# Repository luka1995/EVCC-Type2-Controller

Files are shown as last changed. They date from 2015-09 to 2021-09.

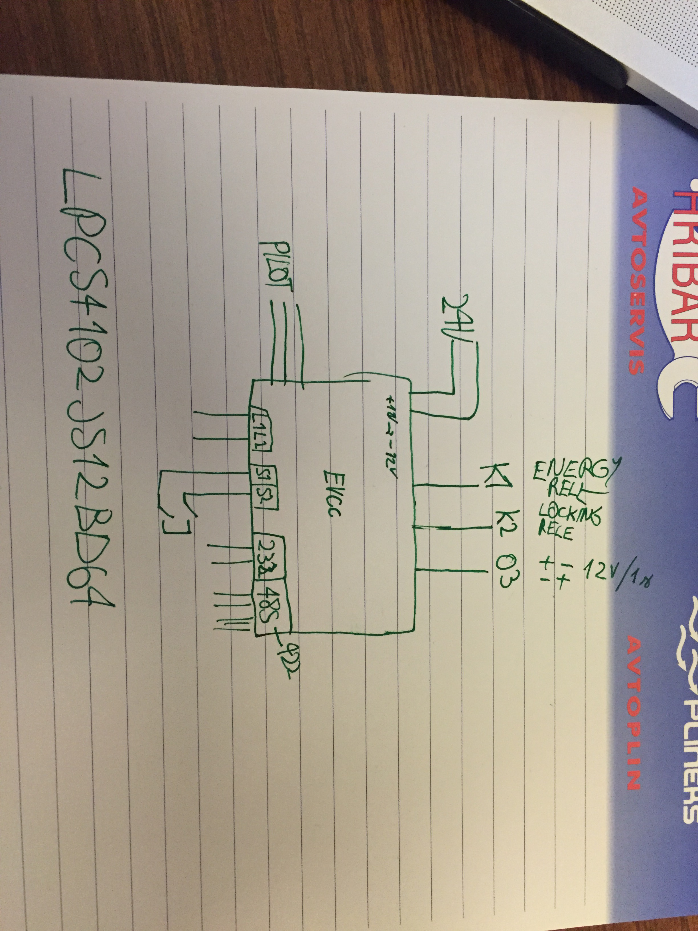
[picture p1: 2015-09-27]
Images/IMG_0896.JPG

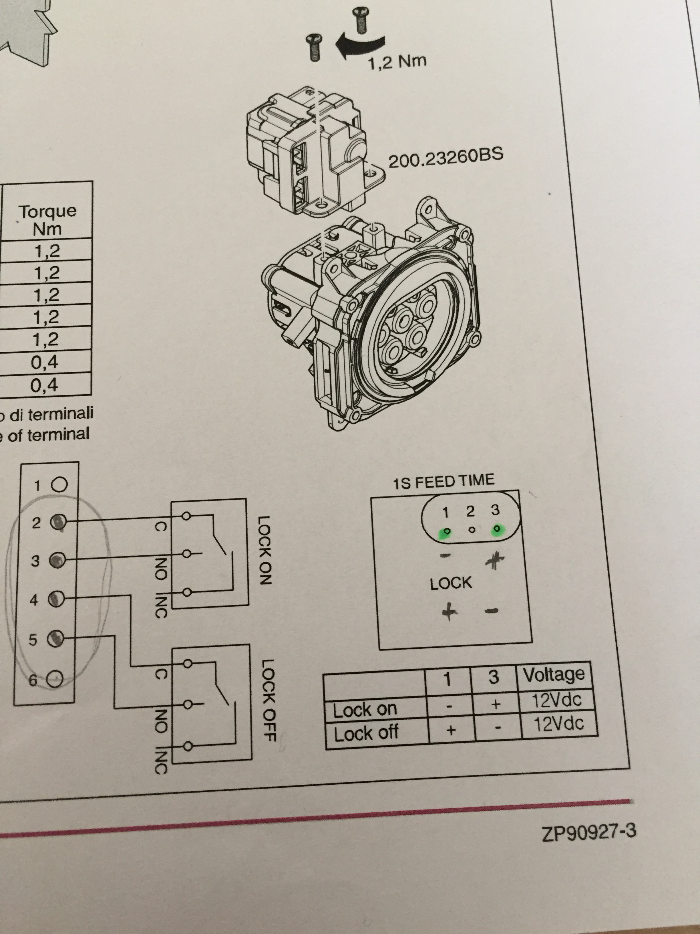
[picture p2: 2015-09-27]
Images/IMG_0889.JPG

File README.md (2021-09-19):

# EVCC TYPE2 Controller

Created by Luka Penger and Duško Cvijič

## Description

The EVCC module controls the power-supply of an electric vehicle (EV) while charging at a supply equipment (EVSE). The communication between EV and EVSE complies with IEC 61851-1 Mode 3.
Potential-free switching contacts are used for load control (EV power-supply) and locking-device (for type 2 socket-outlet). Two external LEDs can be connected without additional resistors and indicate the present system status. Default and available charging current can be set via the RS485 serial interface. The available charging current can be changed while charging, limited by the default current and the rated current of the charging cable (type 2 socket-outlet only).
Start of the charging process and monitoring of the locking mechanism of the socket outlet are controlled by external switches directly connected to the module.
Using the RS485-interface several EVCC can be connected as network with an individual address assigned to each module.

Connector type 2: SAE J1772</br>
Type 2 standard: IEC 61851-1 Mode 3
Serial interface: RS485, 38400Bd, 8 data bits, 1 stop bit, no parity</br>
-> No internal termination; use 120Ω-resistor to terminate both ends of network!

## Proximity voltages:

Max Current
13 A --> Vadc = 2,57 V (R = 1550 ohms)
20 A --> Vadc = 2,22 V (R = 680 ohms)
32 A --> Vadc = 1,82 V (R = 220 ohms)
63 A --> Vadc = 1,66 V (R = 100 ohms)

Not connected --> Vadc = 3.3 V (Max 6A)

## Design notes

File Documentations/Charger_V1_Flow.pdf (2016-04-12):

## Charger Flow V1

Raspberry PI 3
Computer

Type 2 Socket
Connector

Contactor 40A
Switch for energy

Energy Meter
Finder / Class B / 3 Phase

RFID Reader
Mifare / USB
Camera | Ethernet | Wi-Fi
Fuse 3x 40A | Current Circuit Breaker Type B+

EVCC Controller
Type 2

M-Bus Converter
M-Bus to RS-232

Mechanical Fuse
3 x 32A

Main Power
22 kW / 230V

Proximity / Pilot line

Power Supply
230V / 12V

LCD Touch Display
Capacitive / 800 x 480

Fuse 1x 10A

M-Bus

USB Converter
12V / 5V

RS-232

Temperature Sensor
DS18b20

Status Light
SSI

HDMI / USB

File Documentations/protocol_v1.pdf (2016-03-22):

Function | Mode | PC->EVCC | EVCC->PC | Parameter xxxx
Reset device | AM | !n 00 | >n 02 Vx.y | Vx.y Firmware Version
Load factory settings and reset device | AM | !n 01 | >n 02 Vx.y | Vx.y Firmware Version
Get version of firmware | AM | !n 02 | >n 02 Vx.y | Vx.y Firmware Version
Set address of device | AM | !n 03 xxxx | >n 03 | 1…9999
Get address of device | AM | !n 04 | >n 04 xxxx | 1…9999
Get state machine state | AM | !n 05 | >n 05 x | 0 - A1 1 - A2 2 - B1 3 - B2 4 - C1 5 - C2 6 - D1 7 - D2 8 - E 9 - F
Get module mode | AM | !n 06 | >n 06 x | 0 - Auto 1 - Module
Switch mode to MANUAL (Stop charging) | A | !n 07 | >n 07
Switch mode to AUTO (Stop charging) | M | !n 08 | >n 08
Get status of output | AM | !n 09 | >n 09 xx | 0 - all outputs are off 1 - LED1 on 2 - LED2 on 4 - K1 on 8 - K2 on 16 - K3 on …bits
Get status of input | AM | !n 10 | >n 10 x | 0 - non active 1 - S1 active 2 - S2 active 3 - S1 & S2 active …bits
Get ADC value positive pilot | AM | !n 11 | >n 11 xxxx | 0000…4095 U = 0.0xx x xxxx [V]

Commands must end with <CR><LF>.
Answers sent by the module end with <CR><LF>.
n module address (address 0 contacts all modules within the network!).

M state = Manual

A state = Auto

Function | Mode | PC->EVCC | EVCC->PC | Parameter xxxx
Get ADC value negative pilot | AM | !n 12 | >n 12 xxxx | 0000…4095
Get ADC value proximity | AM | !n 13 | >n 13 xxxx | 0000…4095
Get positive pilot voltage | AM | !n 14 | >n 14 xxxx | 0.0…12.0 [V]
Get negative pilot voltage | AM | !n 15 | >n 15 xxxx | 0.0…-12.0 [V]
Get proximity voltage | AM | !n 16 | >n 16 xxxx | 0.0…3.3 [V]
Get Ic - PWM duty cycle | AM | !n 17 | > 17 xxx | 80…970 - PWM value 8%…97%
Set Ic max | M | !n 18 xxx | >n 18 | 0 - 6A 1 - 10A 2 - 13A 3 - 16A 4 - 20A 5 - 32A 6 - 40A 7 - 50A 8 - 60A 9 - 70A 10 - 80A 11 - Idefault 80…970 - PWM value 8%…97%
Set Idefault | M | !n 19 xxx | >n 19 | 0 - 6A 1 - 10A 2 - 13A 3 - 16A 4 - 20A 5 - 32A 6 - 40A 7 - 50A 8 - 60A 9 - 70A 10 - 80A 80…970 - PWM value 8%…97%
Get Idefault | AM | !n 20 | >n 20 xxx | 80…970 - PWM value 8%…97%
Switch PWM on | M | !n 21 | >n 21
Switch PWM off | M | !n 22 | >n 22
Get PWM state | AM | !n 23 | >n 23 x | 0 - OFF 1 - ON
Start charging | M | !n 24 | >n 24
Stop charging | M | !n 25 | >n 25

Function | Mode | PC->EVCC | EVCC->PC | Parameter xxxx
Enable proximity cable detection max current | AM | !n 26 | >n 26
Disable proximity cable detection max current | AM | !n 27 | >n 27
Get proximity cable detection state | AM | !n 28 | >n 28 | 0 - OFF 1 - ON

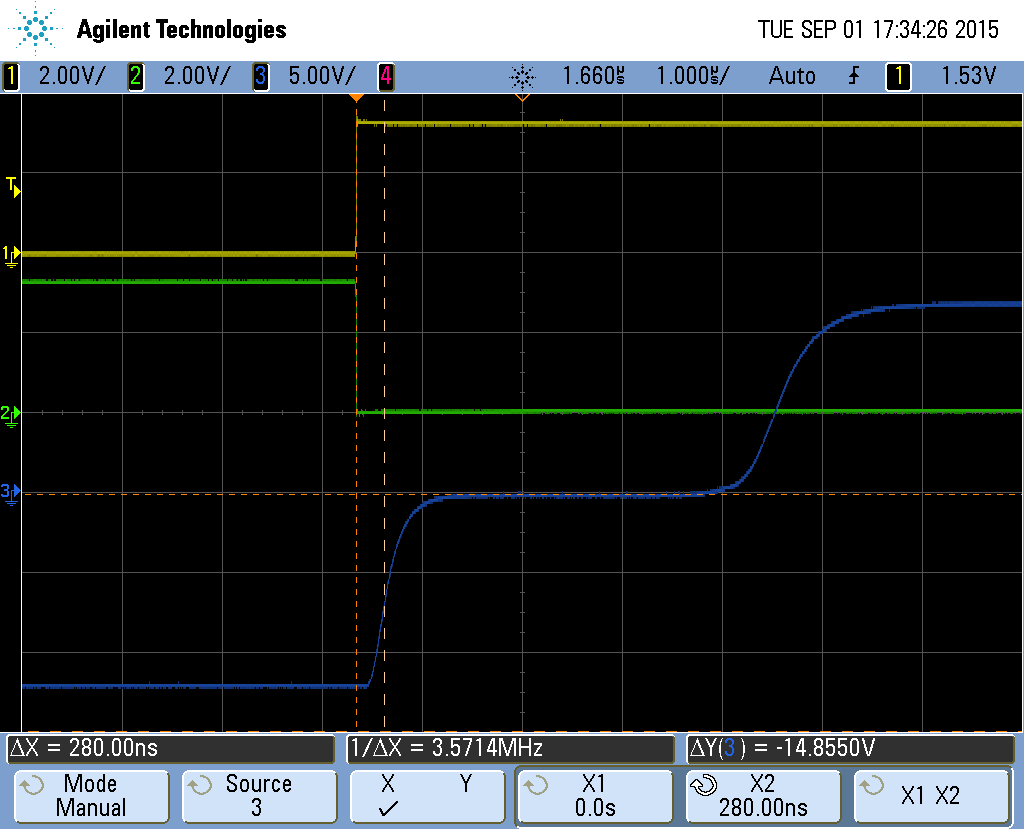
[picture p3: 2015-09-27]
Images/scope_0.bmp

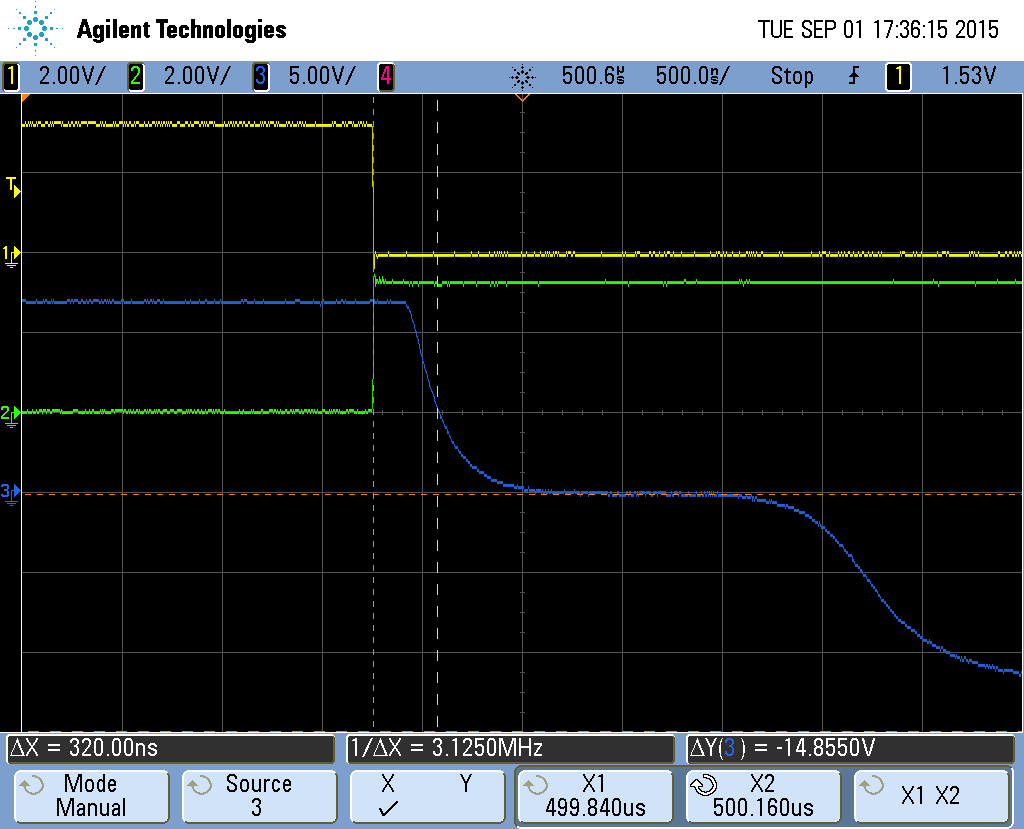
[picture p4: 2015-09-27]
Images/scope_2.bmp

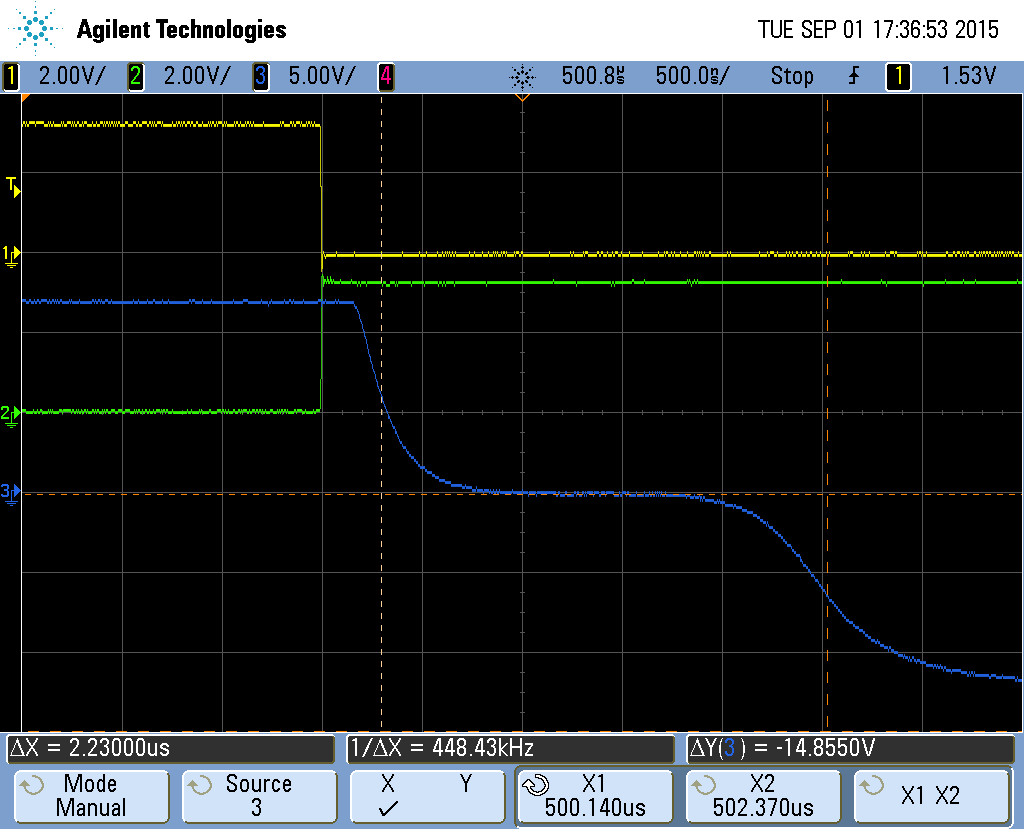
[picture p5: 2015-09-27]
Images/scope_3.bmp

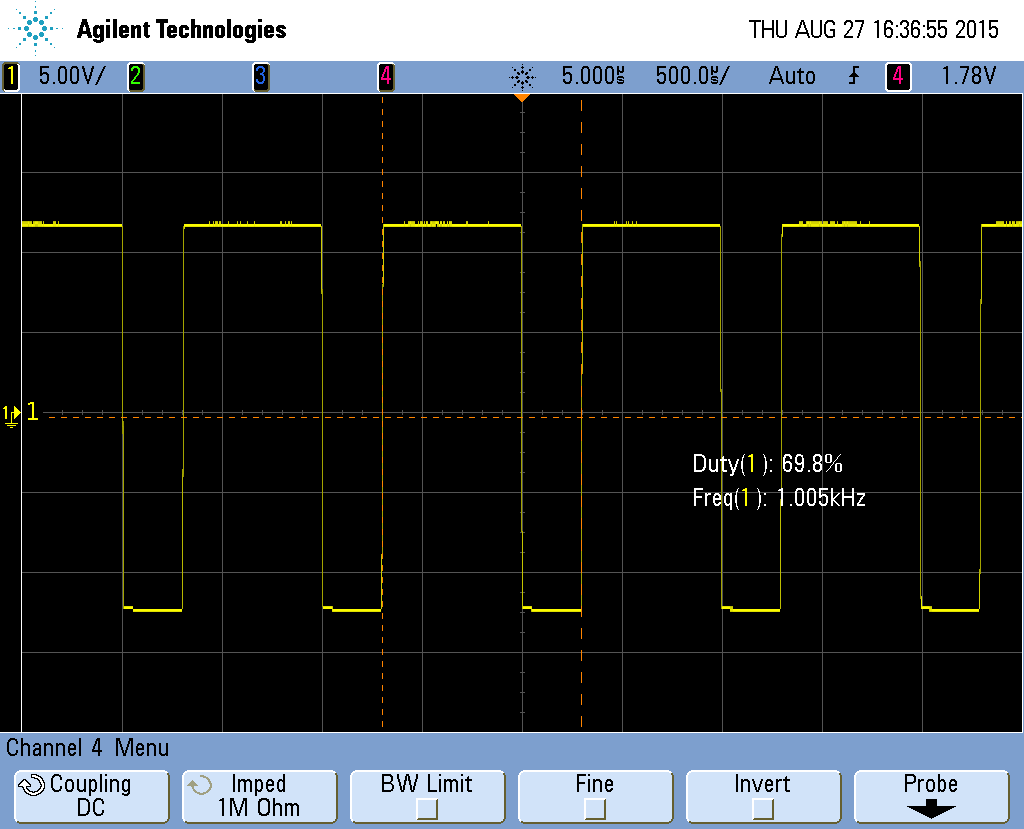
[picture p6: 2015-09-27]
Images/pwm_70.bmp

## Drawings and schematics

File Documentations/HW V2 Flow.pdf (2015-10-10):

## EVCC TYPE2 Controller Hardware V2

### Main power supply

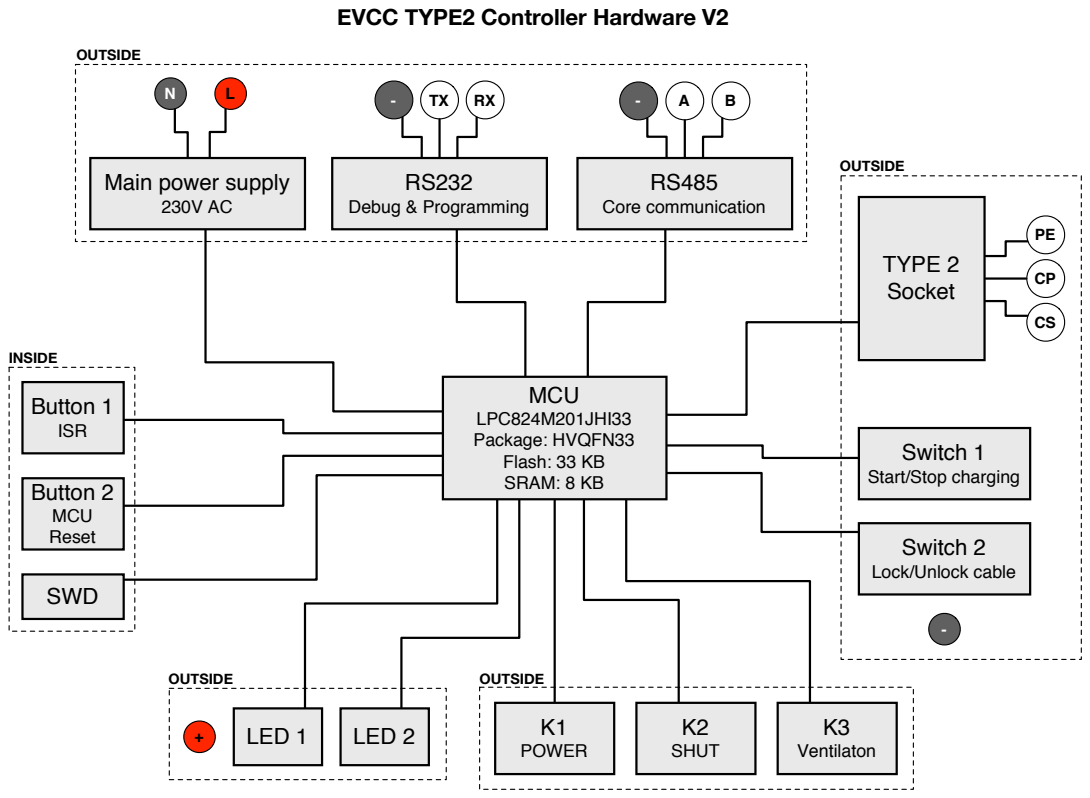
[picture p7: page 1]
MCU LPC824M201JHI33 Package: HVQFN33 Flash: 33 KB SRAM: 8 KB; RS232 Debug & Programming; RS485 Core communication; Button 1 ISR; Button 2 MCU Reset; SWD; TYPE 2 Socket; LED 1; LED 2; K1 POWER; K2 SHUT; K3 Ventilaton; INSIDE; OUTSIDE

Switch 1
Start/Stop charging

Switch 2
Lock/Unlock cable

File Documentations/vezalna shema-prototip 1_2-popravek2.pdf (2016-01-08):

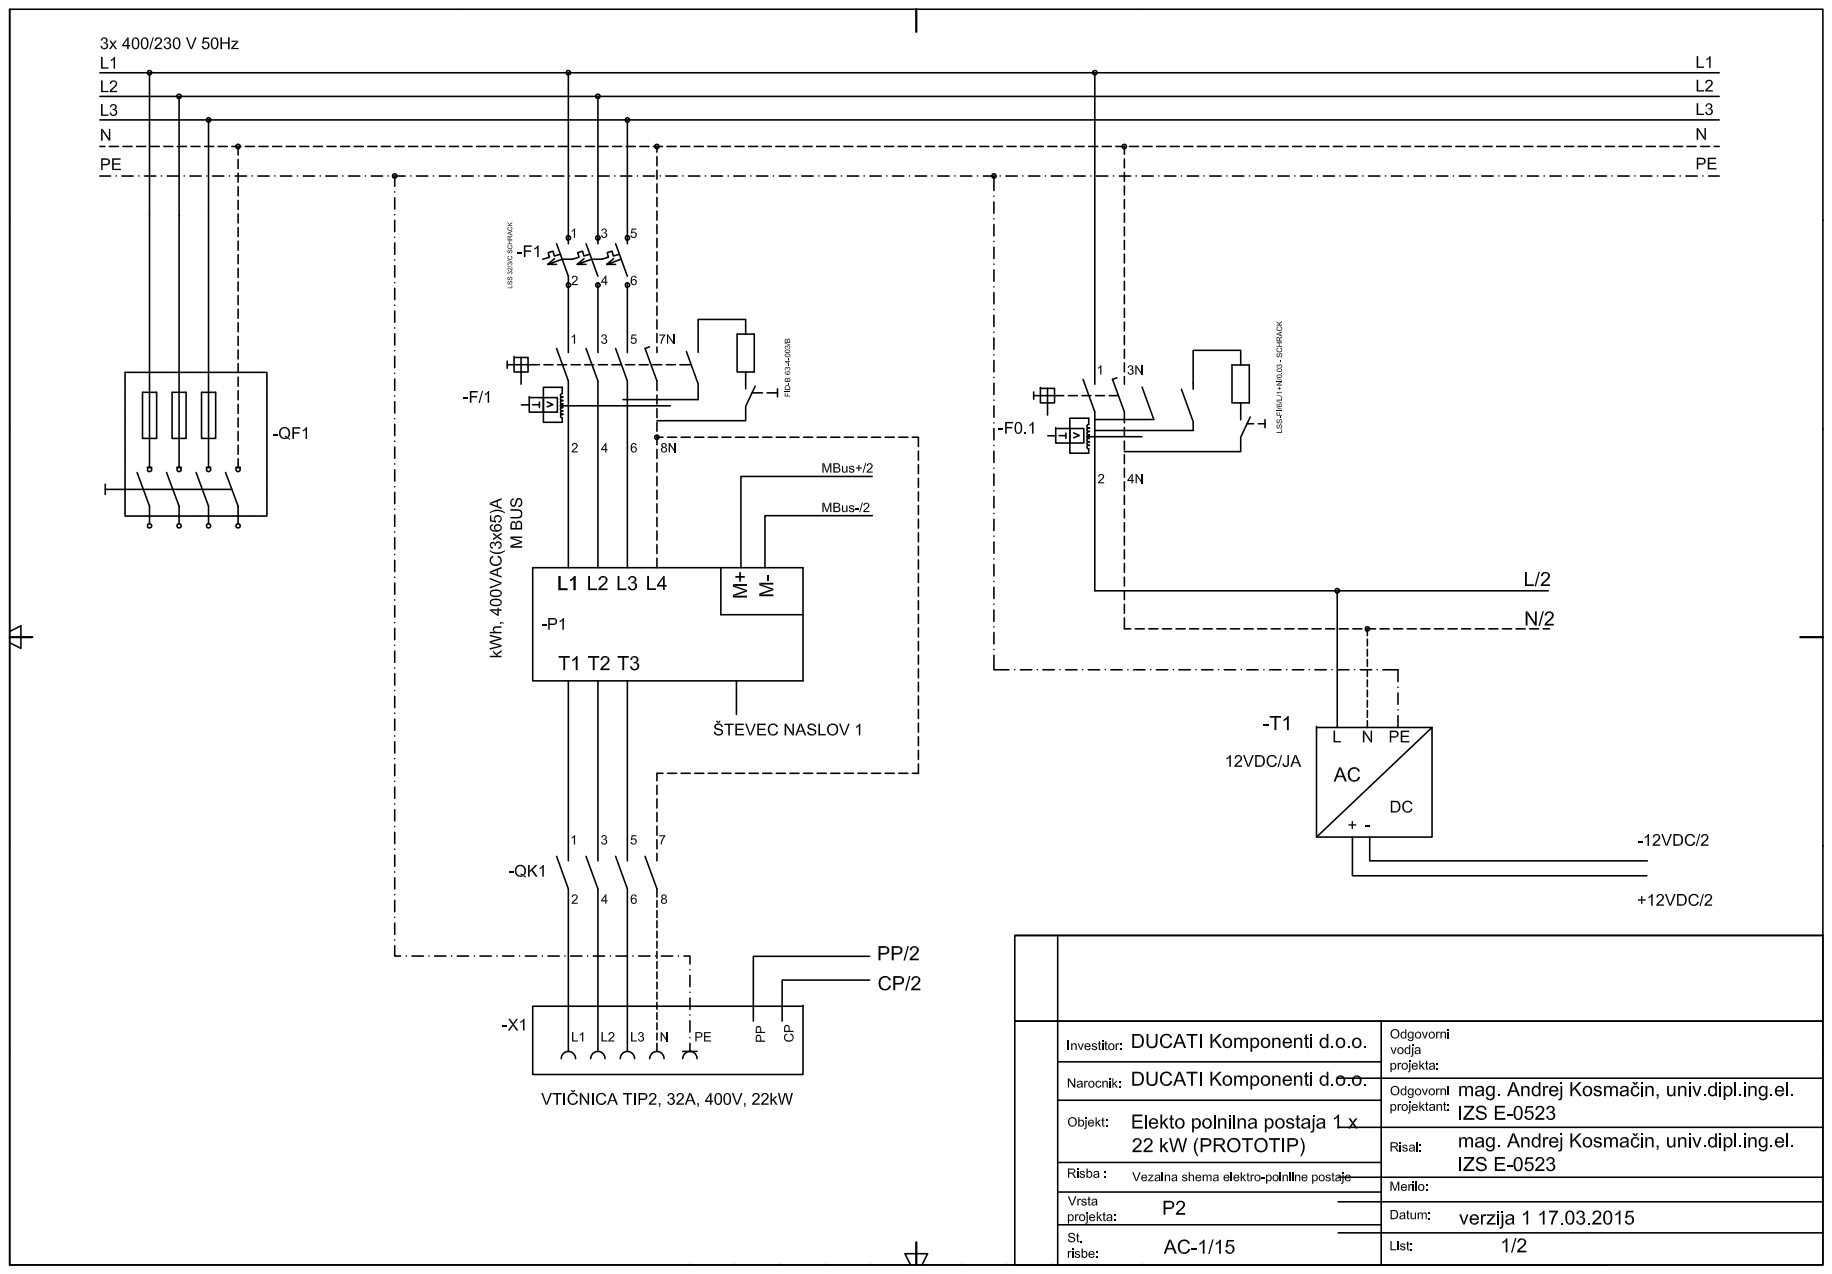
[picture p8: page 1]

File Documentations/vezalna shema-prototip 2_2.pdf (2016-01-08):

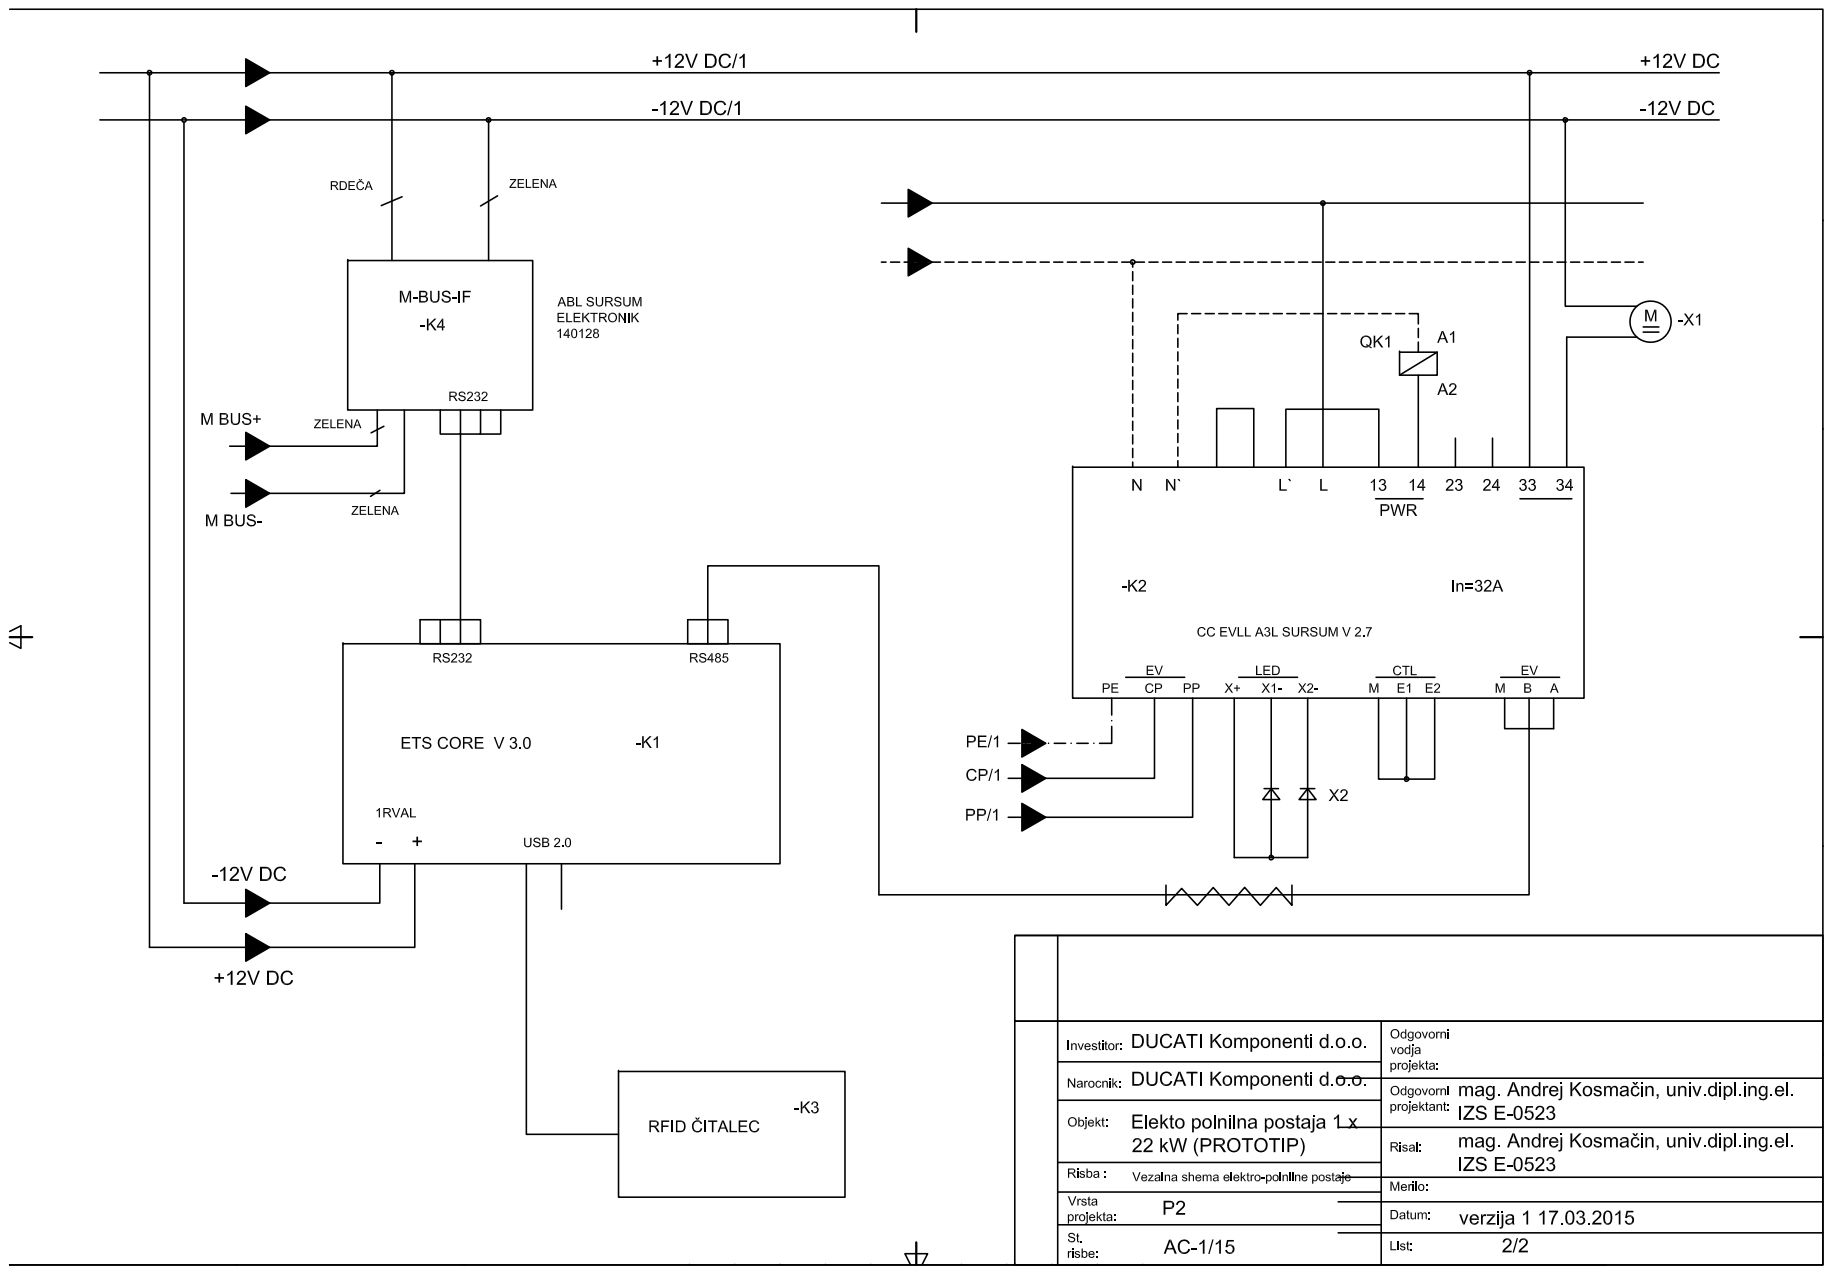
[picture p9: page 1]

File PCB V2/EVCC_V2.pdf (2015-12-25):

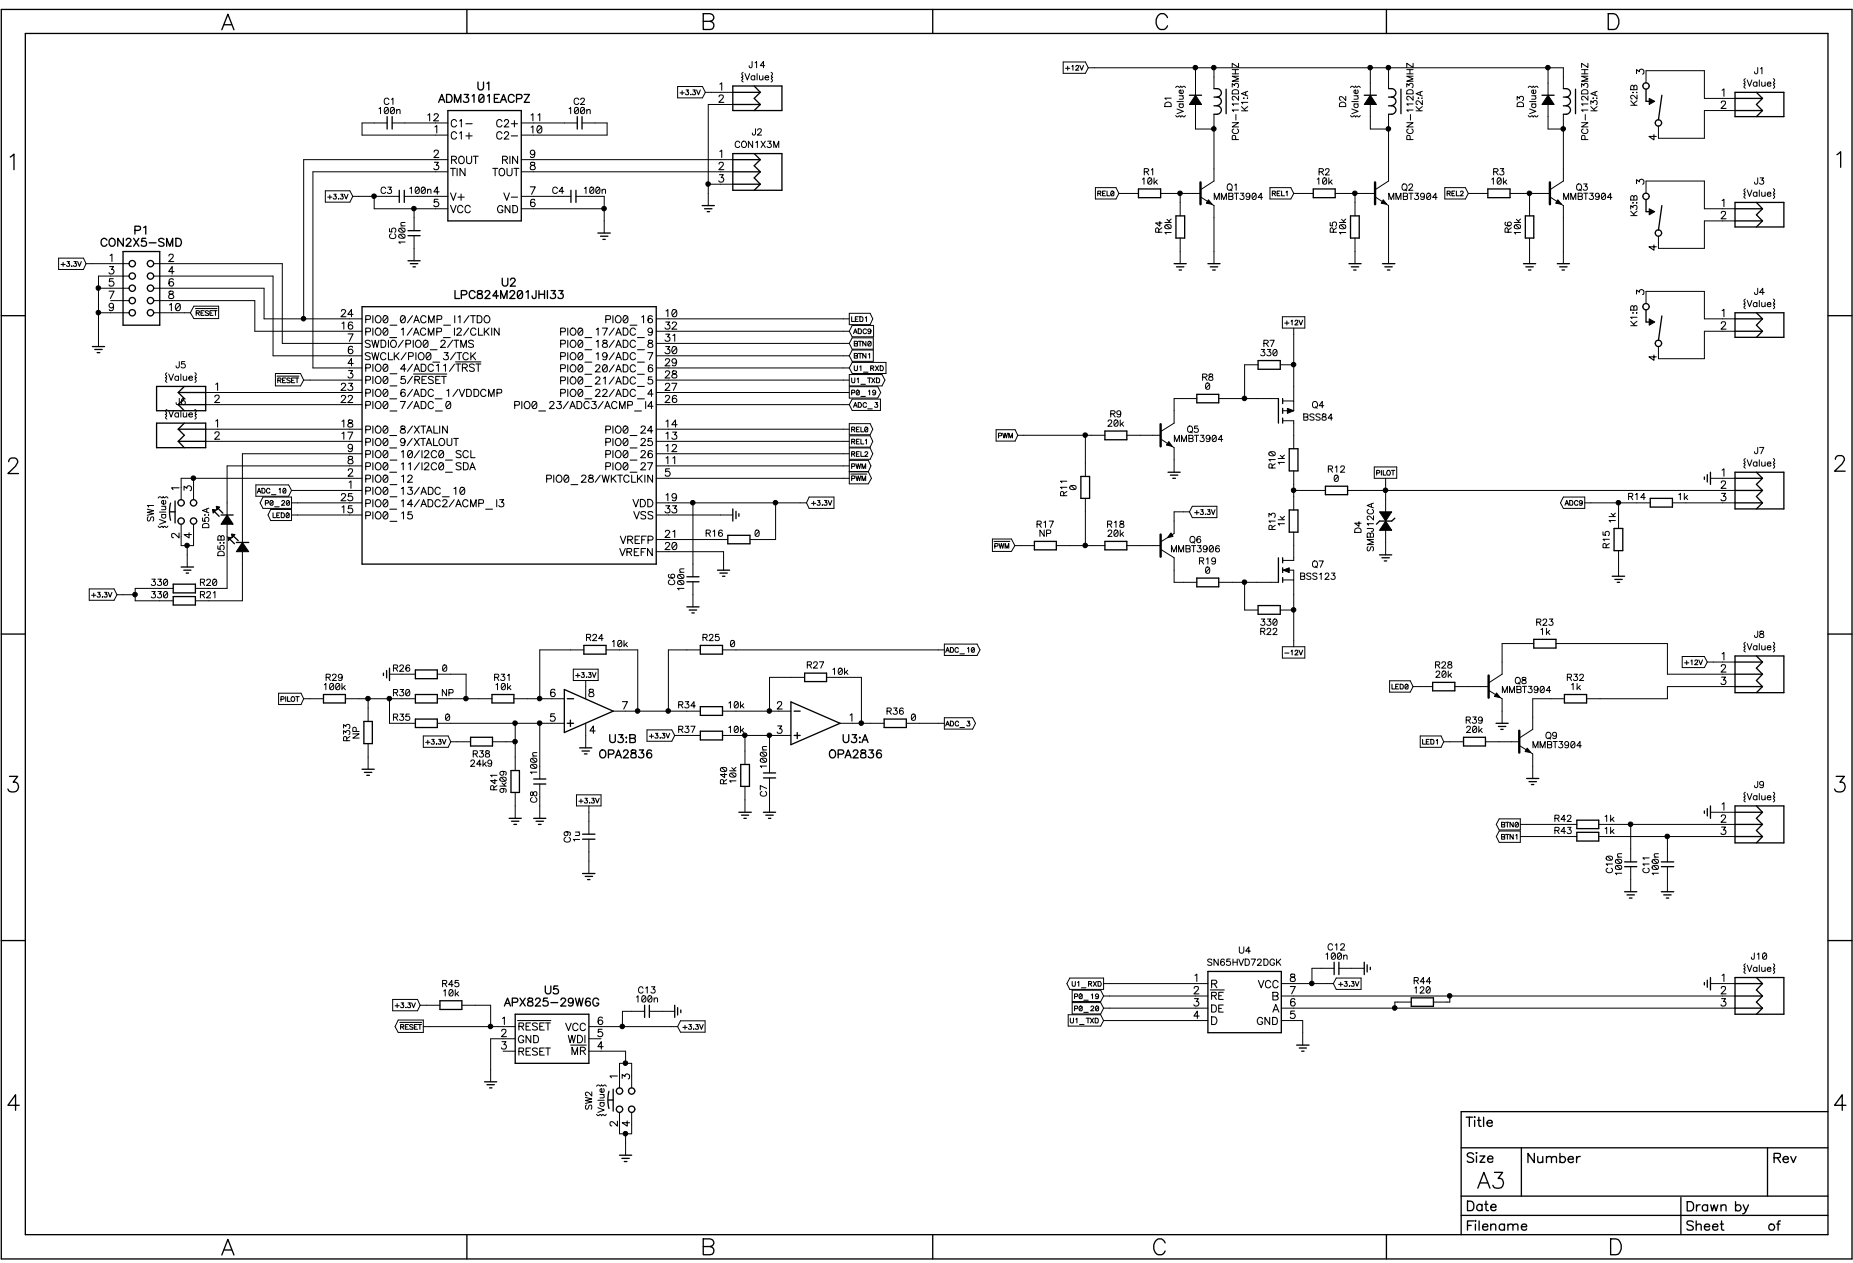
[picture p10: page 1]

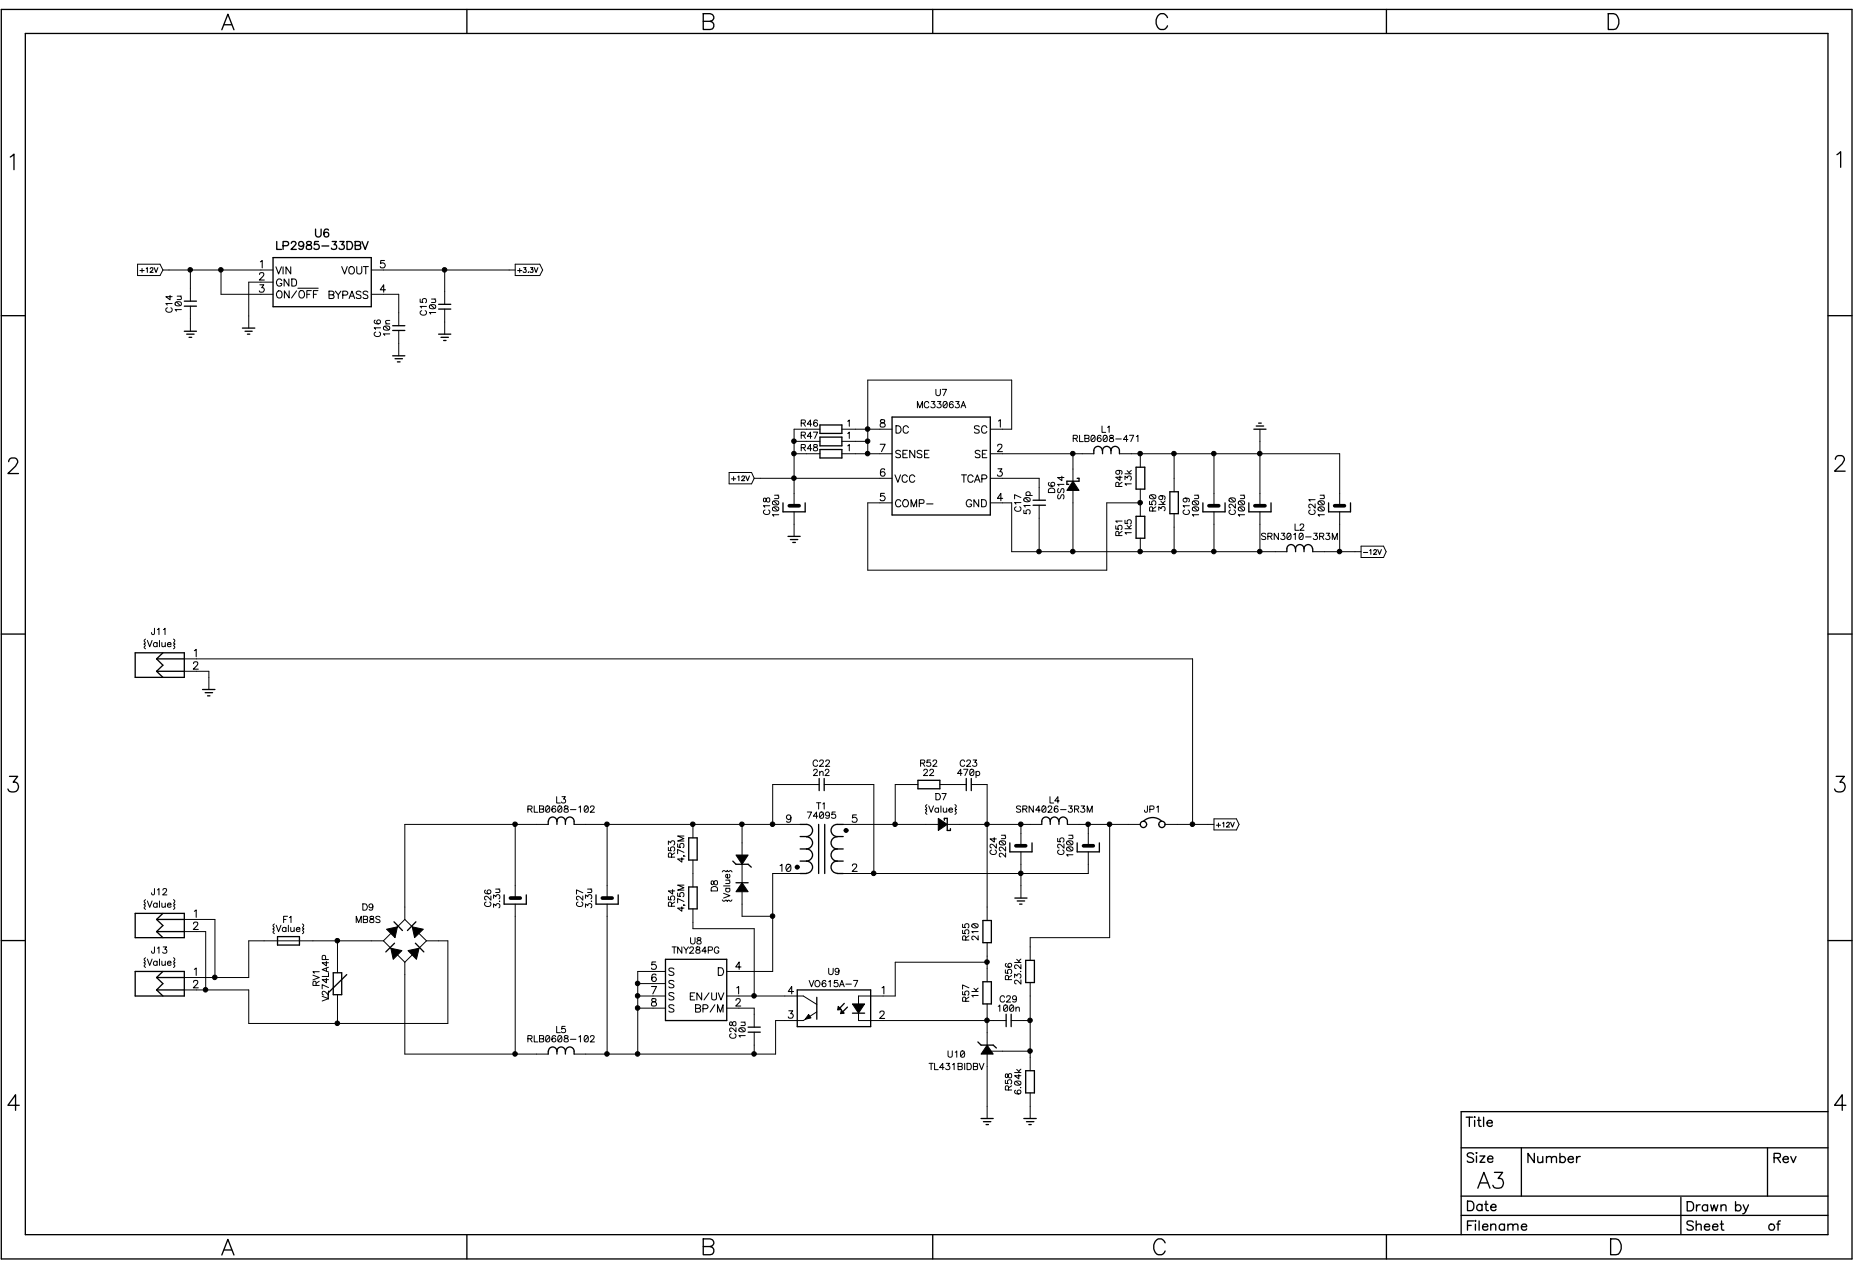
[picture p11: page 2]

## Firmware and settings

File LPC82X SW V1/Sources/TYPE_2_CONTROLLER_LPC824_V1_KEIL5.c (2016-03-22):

/*----------------------------------------------------------------------------
 *      Type 2 Controller LPC824
 *			Copyright 2015
 *			Luka Penger
 *			Avant Car d.o.o.
 *---------------------------------------------------------------------------*/

#include <stdio.h>
#include <stdint.h>
#include <stdbool.h>
#include <stddef.h>
#include <ctype.h>
#include <LPC82x.h>

#include "cmsis_os.h"
#include <GPIO_LPC82x.h>
#include <ADC_LPC82x.h>
#include <IAP_LPC82x.h>
#include <WWDT_LPC82x.h>
#include "SETTINGS.h"
#include "EV_UART.h"
#include "EV_PWM.h"
#include "EV_ADC.h"
#include "EV_STATE_MACHINE.h"
#include "EV_OUTPUTS.h"
#include "EV_INPUTS.h"

/*****************************************************************************
 * Definitions
 ****************************************************************************/

#define FIRMWARE_VERSION												"1.0"

#define DEFAULT_MODULE_ADDRESS									0
#define MODULE_ADDRESS_MAX_NUMBER								9999

#define ADC_SAMPLE_INTERVAL											100 // ms / when pwm = false
#define STATE_MACHINE_INTERVAL									50 // ms

/*****************************************************************************
 * Public variables
 ****************************************************************************/

extern SETTINGS_Struct settingsData;

extern EvModuleMode selectedModuleMode;

extern char EV_UART_Buffer[EV_UART_BUFFER_SIZE];
extern int EV_UART_BufferLength;
extern bool EV_UART_DataReceived;

extern float selectedMaximumCurrent;
extern bool pwmRunning;
extern float evPwmDutyCycle;

extern bool sequenceAComplete, sequenceBComplete;
extern bool groundError;
extern unsigned int proximityADCValue; // 0 - 4095
extern unsigned int pilotPositiveADCValue; // 0 - 4095
extern unsigned int pilotNegativeADCValue; // 0 - 4095
extern float proximityVoltage; // 0.0V - 3.3V
extern float pilotPositiveVoltage; // 0.0V - 12.0V
extern float pilotNegativeVoltage; // 0.0V - -12.0V
extern bool adcCPVoltageMeasured, adcPPVoltageMeasured;

extern void (*currentStateMachine)(void);
extern int evStateMachineWaitMs;
extern bool manualStartChargingFlag;

int ledWaitMs = 0;

/*****************************************************************************
 * Watchdog Timer
 ****************************************************************************/

void WDT_IRQHandler(void) {
	uint32_t wdtStatus = WWDT_GetStatus(LPC_WWDT);
	
	/* The chip will reset before this happens, but if the WDT doesn't
	   have WWDT_WDMOD_WDRESET enabled, this will hit once */
	if (wdtStatus & WWDT_WDMOD_WDTOF) {
		/* A watchdog feed didn't occur prior to window timeout */
		WWDT_UnsetOption(LPC_WWDT, WWDT_WDMOD_WDEN);	/* Stop WDT */
		WWDT_ClearStatusFlag(LPC_WWDT, WWDT_WDMOD_WDTOF);
		WWDT_Start(LPC_WWDT);	/* Needs restart */
	}

	/* Handle warning interrupt */
	if (wdtStatus & WWDT_WDMOD_WDINT) {
		/* A watchdog feed didn't occur prior to warning timeout */
		WWDT_ClearStatusFlag(LPC_WWDT, WWDT_WDMOD_WDINT);
		WWDT_Feed(LPC_WWDT);
	}
}

void Watchdog_Init(void) {
	uint32_t wdtFreq;
	
	/* Freq = 0.6Mhz, divided by 64. WDT_OSC should be 9.375khz */
	Clock_SetWDTOSC(WDTLFO_OSC_0_60, 64);
	
	SYSCTL_PowerUp(SYSCTL_SLPWAKE_WDTOSC_PD);

	wdtFreq = (Clock_GetWDTOSCRate() / 4);
	
	WWDT_Init(LPC_WWDT);

	/* Set watchdog feed time constant to approximately 2s
	   Set watchdog warning time to 512 ticks after feed time constant
	   Set watchdog window time to 3s */
	WWDT_SetTimeOut(LPC_WWDT, wdtFreq * 2);
	WWDT_SetWarning(LPC_WWDT, 512);
	WWDT_SetWindow(LPC_WWDT, wdtFreq * 3);

	/* Configure WWDT to reset on timeout */
	WWDT_SetOption(LPC_WWDT, WWDT_WDMOD_WDRESET);

	/* Clear watchdog warning and timeout interrupts */
	WWDT_ClearStatusFlag(LPC_WWDT, WWDT_WDMOD_WDTOF | WWDT_WDMOD_WDINT);

	/* Clear and enable watchdog interrupt */
	NVIC_ClearPendingIRQ(WDT_IRQn);
	NVIC_EnableIRQ(WDT_IRQn);

	/* Start watchdog */
	WWDT_Start(LPC_WWDT);
}

/*****************************************************************************
 * Public functions
 ****************************************************************************/


/*****************************************************************************
 * Private functions
 ****************************************************************************/

void init(void) {
	SystemInit();
	SystemCoreClockUpdate();
	
	/*
	1 = 1s
	10 = 100ms
	100 = 10ms
	1000 = 1ms*/
	SysTick_Config(SystemCoreClock / 1000);
	
	// WWDT Init
	
	Watchdog_Init();
	
	// EV Init
	
	EV_OUTPUTS_Init();
	
	EV_INPUTS_Init();

	EV_UART_Init();
	
	EV_PWM_Init();
	
	EV_ADC_Init();
	
	// Settings load
	
	SETTINGS_Load();
	
	// Default state machine
	
	EV_State_A1();
}

/*****************************************************************************
 * Main
 ****************************************************************************/

int main(void) {
	//
	// Variables
	//
	char *evUartModuleAddressString = NULL, *evUartFunctionString = NULL, *evUartValueString = NULL;
	int evUartModuleAddressSpaceIndex = 0, evUartFunctionSpaceIndex = 0;
	int evUartModuleAddressNumber = 0, evUartFunctionNumber = 0, evUartValueNumber = 0;
	bool evUartShowCommandError = false;
	int sysTickAdcSampleValue = 0, sysTickStateMachineValue = 0;
	
	//
	// Init
	//
 	init();
	
	// Send firmware version
	
	EV_UART_SendStringFormat("%c%d %02d", EV_UART_SEND_CHARACTER, settingsData.selectedModuleAddress, 2);
	EV_UART_SendString(" V"FIRMWARE_VERSION);
	EV_UART_SendString("\r\n");
	
	// Set maximum current
	
	selectedMaximumCurrent = settingsData.selectedIdefault;
	EV_PWM_SetDutyCycle(selectedMaximumCurrent);
	
	//
	// While
	//
	while (1) {
		/*****************************************************************************
		* ADC Voltage Read
		****************************************************************************/
		
		if (sequenceAComplete == true) {
			sequenceAComplete = false; // Clear flag
			
			// Read CP Voltage
			
			EV_ADC_ReadCPVoltage();
	  }
		
		if (sequenceBComplete == true) {
			sequenceBComplete = false; // Clear flag
			
			// Read PP Voltage
			
			EV_ADC_ReadPPVoltage();
	  }
		
		/*****************************************************************************
		* SysTick Value Listener
		****************************************************************************/

		if (SysTick->CTRL & SysTick_CTRL_COUNTFLAG_Msk) {
			// ADC Sequencer
			
			if (sysTickAdcSampleValue >= ADC_SAMPLE_INTERVAL) {
				sysTickAdcSampleValue = 0; // Clear flag

				if (pwmRunning == false) {
					ADC_StartSequencer(LPC_ADC, ADC_SEQA_IDX);
				}
				
				ADC_StartSequencer(LPC_ADC, ADC_SEQB_IDX);
			} else {
				sysTickAdcSampleValue++;
			}
			
			// EV State Machine
			
			if (adcCPVoltageMeasured && sysTickStateMachineValue >= STATE_MACHINE_INTERVAL) {
				sysTickStateMachineValue = 0; // Clear flag

				// State machine
			
				EV_State_Machine();
			} else {
				sysTickStateMachineValue++;
			}
			
			if (evStateMachineWaitMs > 0) {
				evStateMachineWaitMs--;
			}
			
			// LED States
			
			if (ledWaitMs == 0) {
				if (currentStateMachine == EV_State_A1 || currentStateMachine == EV_State_A2) {
					ledWaitMs = 1000; // Only for disable setting led no 1ms
					
					EV_OUTPUTS_SetLED2(false);
					EV_OUTPUTS_SetLED1(false);
				} else if (currentStateMachine == EV_State_B1 || currentStateMachine == EV_State_B2) {
					ledWaitMs = 1000; // Only for disable setting led no 1ms
					
					EV_OUTPUTS_SetLED2(false);
					EV_OUTPUTS_SetLED1(true);
				} else if (currentStateMachine == EV_State_C1 || currentStateMachine == EV_State_C2) {
					ledWaitMs = 1000; // Only for disable setting led no 1ms
					
					EV_OUTPUTS_SetLED2(true);
					EV_OUTPUTS_SetLED1(false);
				} else if (currentStateMachine == EV_State_D1 || currentStateMachine == EV_State_D2) {
					ledWaitMs = 1000;
					
					EV_OUTPUTS_SetLED1(false);
					
					if (EV_OUTPUTS_GetStateLED2()) {
						EV_OUTPUTS_SetLED2(false);
					} else {
						EV_OUTPUTS_SetLED2(true);
					}
				} else if (currentStateMachine == EV_State_E || currentStateMachine == EV_State_F) {
					ledWaitMs = 2000;
					
					if (EV_OUTPUTS_GetStateLED1()) {
						EV_OUTPUTS_SetLED2(false);
						EV_OUTPUTS_SetLED1(false);
					} else {
						EV_OUTPUTS_SetLED2(true);
						EV_OUTPUTS_SetLED1(true);
					}
				}
			} else {
				ledWaitMs--;
			}
		}
		
		/*****************************************************************************
		* EV UART Listener
		****************************************************************************/
		
		if (EV_UART_DataReceived == true && (UART_GetStatus(EV_UART) & UART_STAT_RXIDLE) != 0 && (UART_GetStatus(EV_UART) & UART_STAT_RXRDY) == 0) {
			EV_UART_DataReceived = false;

			// Search MODULE ADDRESS space index
			evUartModuleAddressSpaceIndex = EV_UART_LocateCharacter(EV_UART_Buffer, EV_UART_BufferLength, 0x20, 0);
			
			if (evUartModuleAddressSpaceIndex > 0) {
				evUartModuleAddressString = (char *)malloc(evUartModuleAddressSpaceIndex);
				strncpy(evUartModuleAddressString, EV_UART_Buffer, evUartModuleAddressSpaceIndex);
				
				if (EV_UART_BufferIsNumber(evUartModuleAddressString, evUartModuleAddressSpaceIndex) == true) {
					evUartModuleAddressNumber = atoi(evUartModuleAddressString);
					
					// Free pointer
					if (evUartModuleAddressString != NULL) { free(evUartModuleAddressString); evUartModuleAddressString = NULL; }
					
					// Check module address if correct
					if (evUartModuleAddressNumber == DEFAULT_MODULE_ADDRESS || evUartModuleAddressNumber == settingsData.selectedModuleAddress) {
						// MODULE ADDRESS IS CORRECT

						// Search FUNCTION space index
						evUartFunctionSpaceIndex = EV_UART_LocateCharacter(EV_UART_Buffer, EV_UART_BufferLength, 0x20, 1);
						
						if (evUartFunctionSpaceIndex > 0) {
							evUartFunctionString = (char *)malloc(evUartFunctionSpaceIndex - (evUartModuleAddressSpaceIndex + 1));
							strncpy(evUartFunctionString, EV_UART_Buffer + (evUartModuleAddressSpaceIndex + 1), (evUartFunctionSpaceIndex - (evUartModuleAddressSpaceIndex + 1)));
							
							// COMMAND WITH VALUE
							if (EV_UART_BufferIsNumber(evUartFunctionString, (evUartFunctionSpaceIndex - (evUartModuleAddressSpaceIndex + 1))) == true) {
								evUartFunctionNumber = atoi(evUartFunctionString);
								
								// Free pointer
								if (evUartFunctionString != NULL) { free(evUartFunctionString); evUartFunctionString = NULL; }
								
								// Search VALUE
								evUartValueString = (char *)malloc(EV_UART_BufferLength - (evUartFunctionSpaceIndex + 1));
								strncpy(evUartValueString, EV_UART_Buffer + (evUartFunctionSpaceIndex + 1), (EV_UART_BufferLength - (evUartFunctionSpaceIndex + 1)));
							
								if (EV_UART_BufferIsNumber(evUartValueString, (EV_UART_BufferLength - (evUartFunctionSpaceIndex + 1))) == true) {
									evUartValueNumber = atoi(evUartValueString);
								
									// Free pointer
									if (evUartValueString != NULL) { free(evUartValueString); evUartValueString = NULL; }
	
									// Functions
									
									switch (evUartFunctionNumber) {
										case kEvUartCommandSetAddressDevice: { // SET ADDRESS OF DEVICE
											if (evUartValueNumber >= 1 && evUartValueNumber >= MODULE_ADDRESS_MAX_NUMBER) {
												settingsData.selectedModuleAddress = evUartValueNumber;
												
												SETTINGS_Save();
												
												EV_UART_SendStringFormat("%c%d %02d", EV_UART_SEND_CHARACTER, settingsData.selectedModuleAddress, evUartFunctionNumber);
												EV_UART_SendString("\r\n");
											} else { // VALUE NOT CORRECT
												evUartShowCommandError = true;
											}
											break;
										}
										case kEvUartCommandSetIcMax: { // SET Ic MAX
											if (evUartValueNumber >= 0 && evUartValueNumber <= (EV_PWM_MAXIMUM_DUTY_CICLE * 10)) {
												switch (evUartValueNumber) {
													case 0: { // 6A
														EV_PWM_SetDutyCycle(EV_CURRENT_PWM_DUTY_6A);
														break;
													}
													case 1: { // 10A
														EV_PWM_SetDutyCycle(EV_CURRENT_PWM_DUTY_10A);
														break;
													}
													case 2: { // 13A
														EV_PWM_SetDutyCycle(EV_CURRENT_PWM_DUTY_13A);
														break;
													}
													case 3: { // 16A
														EV_PWM_SetDutyCycle(EV_CURRENT_PWM_DUTY_16A);
														break;
													}
													case 4: { // 20A
														EV_PWM_SetDutyCycle(EV_CURRENT_PWM_DUTY_20A);
														break;
													}
													case 5: { // 32A
														EV_PWM_SetDutyCycle(EV_CURRENT_PWM_DUTY_32A);
														break;
													}
													case 6: { // 40A
														EV_PWM_SetDutyCycle(EV_CURRENT_PWM_DUTY_40A);
														break;
													}
													case 7: { // 50A
														EV_PWM_SetDutyCycle(EV_CURRENT_PWM_DUTY_50A);
														break;
													}
													case 8: { // 60A
														EV_PWM_SetDutyCycle(EV_CURRENT_PWM_DUTY_60A);
														break;
													}
													case 9: { // 70A
														EV_PWM_SetDutyCycle(EV_CURRENT_PWM_DUTY_70A);
														break;
													}
													case 10: { // 80A
														EV_PWM_SetDutyCycle(EV_CURRENT_PWM_DUTY_80A);
														break;
													}
													case 11: { // Idefault
														EV_PWM_SetDutyCycle(settingsData.selectedIdefault);
														break;
													}
													default: {
														EV_PWM_SetDutyCycle((float)((float)evUartValueNumber / 10));
														break;
													}
												}
												
												EV_UART_SendStringFormat("%c%d %02d", EV_UART_SEND_CHARACTER, settingsData.selectedModuleAddress, evUartFunctionNumber);
												EV_UART_SendString("\r\n");
											} else { // VALUE NOT CORRECT
												evUartShowCommandError = true;
											}
											break;
										}
										case kEvUartCommandSetIDefault: { // SET Idefault
											if (evUartValueNumber >= 0 && evUartValueNumber <= (EV_PWM_MAXIMUM_DUTY_CICLE * 10)) {
												switch (evUartValueNumber) {
													case 0: { // 6A
														settingsData.selectedIdefault = EV_CURRENT_PWM_DUTY_6A;
														break;
													}
													case 1: { // 10A
														settingsData.selectedIdefault = EV_CURRENT_PWM_DUTY_10A;
														break;
													}
													case 2: { // 13A
														settingsData.selectedIdefault = EV_CURRENT_PWM_DUTY_13A;
														break;
													}
													case 3: { // 16A
														settingsData.selectedIdefault = EV_CURRENT_PWM_DUTY_16A;
														break;
													}
													case 4: { // 20A
														settingsData.selectedIdefault = EV_CURRENT_PWM_DUTY_20A;
														break;
													}
													case 5: { // 32A
														settingsData.selectedIdefault = EV_CURRENT_PWM_DUTY_32A;
														break;
													}
													case 6: { // 40A
														settingsData.selectedIdefault = EV_CURRENT_PWM_DUTY_40A;
														break;
													}
													case 7: { // 50A
														settingsData.selectedIdefault = EV_CURRENT_PWM_DUTY_50A;
														break;
													}
													case 8: { // 60A
														settingsData.selectedIdefault = EV_CURRENT_PWM_DUTY_60A;
														break;
													}
													case 9: { // 70A
														settingsData.selectedIdefault = EV_CURRENT_PWM_DUTY_70A;
														break;
													}
													case 10: { // 80A
														settingsData.selectedIdefault = EV_CURRENT_PWM_DUTY_80A;
														break;
													}
													default: {
														settingsData.selectedIdefault = (float)((float)evUartValueNumber / 10);
														break;
													}
												}
												
												SETTINGS_Save();
												
												EV_UART_SendStringFormat("%c%d %02d", EV_UART_SEND_CHARACTER, settingsData.selectedModuleAddress, evUartFunctionNumber);
												EV_UART_SendString("\r\n");
											} else { // VALUE NOT CORRECT
												evUartShowCommandError = true;
											}
											break;
										}
										default: { // THIS FUNCTION DOESNT EXISTS
											evUartShowCommandError = true;
											break;
										}
									}
								} else { // VALUE NOT CORRECT
									evUartShowCommandError = true;
								}
							} else { // FUNCTION NOT CORRECT
								evUartShowCommandError = true;
							}
						} else {
							evUartFunctionString = (char *)malloc(EV_UART_BufferLength - (evUartModuleAddressSpaceIndex + 1));
							strncpy(evUartFunctionString, EV_UART_Buffer + (evUartModuleAddressSpaceIndex + 1), (EV_UART_BufferLength - (evUartModuleAddressSpaceIndex + 1)));
							
							// COMMAND WITHOUT VALUE
							if (EV_UART_BufferIsNumber(evUartFunctionString, (EV_UART_BufferLength - (evUartModuleAddressSpaceIndex + 1))) == true) {
								evUartFunctionNumber = atoi(evUartFunctionString);
								
								// Free pointer
								if (evUartFunctionString != NULL) { free(evUartFunctionString); evUartFunctionString = NULL; }
	
								// Functions
								
								switch (evUartFunctionNumber) {
									case kEvUartCommandResetDevice: { // RESET DEVICE
										NVIC_SystemReset();
										break;
									}
									case kEvUartCommandLoadFactorySettings: { // LOAD FACTORY SETTINGS AND RESET DEVICE
										SETTINGS_LoadFactorySettings();
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

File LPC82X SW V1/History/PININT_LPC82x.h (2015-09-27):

/****************************************************************************
	Luka Penger 2015
	PIN INT LPC82x
****************************************************************************/
#ifndef __PININT_LPC82x_H 
#define __PININT_LPC82x_H

#include <LPC82x.h>
#include <stdbool.h>

/* Reserved bits masks for registers */
#define PININT_ISEL_RESERVED    (~0xff)
#define PININT_IENR_RESERVED    (~0xff)
#define PININT_SIENR_RESERVED   (~0xff)
#define PININT_CIENR_RESERVED   (~0xff)
#define PININT_IENF_RESERVED    (~0xff)
#define PININT_SIENF_RESERVED   (~0xff)
#define PININT_CIENF_RESERVED   (~0xff)
#define PININT_RISE_RESERVED    (~0xff)
#define PININT_FALL_RESERVED    (~0xff)
#define PININT_IST_RESERVED     (~0xff)
#define PININT_PMCTRL_RESERVED  (~0xff000003)
#define PININT_PMSRC_RESERVED   0xff
#define PININT_PMCFG_RESERVED   (1<<7)

/**
 * LPC8xx Pin Interrupt and Pattern match engine register
 * bit fields and macros
 */
/* PININT interrupt control register */
#define PININT_PMCTRL_PMATCH_SEL (1 << 0) 
#define PININT_PMCTRL_RXEV_ENA   (1 << 1) 

/* PININT Bit slice source register bits */
#define PININT_SRC_BITSOURCE_START  8
#define PININT_SRC_BITSOURCE_MASK   7

/* PININT Bit slice configuration register bits */
#define PININT_SRC_BITCFG_START  8
#define PININT_SRC_BITCFG_MASK   7

/**
 * LPC8xx Pin Interrupt channel values
 */
#define PININTCH0         (1 << 0)
#define PININTCH1         (1 << 1)
#define PININTCH2         (1 << 2)
#define PININTCH3         (1 << 3)
#define PININTCH4         (1 << 4)
#define PININTCH5         (1 << 5)
#define PININTCH6         (1 << 6)
#define PININTCH7         (1 << 7)
#define PININTCH(ch)      (1 << (ch))

/**
 * LPC8xx Pin Matching Interrupt bit slice enum values
 */
typedef enum PININT_BITSLICE {
	PININTBITSLICE0 = 0,	/*!< PININT Bit slice 0 */
	PININTBITSLICE1 = 1,	/*!< PININT Bit slice 1 */
	PININTBITSLICE2 = 2,	/*!< PININT Bit slice 2 */
	PININTBITSLICE3 = 3,	/*!< PININT Bit slice 3 */
	PININTBITSLICE4 = 4,	/*!< PININT Bit slice 4 */
	PININTBITSLICE5 = 5,	/*!< PININT Bit slice 5 */
	PININTBITSLICE6 = 6,	/*!< PININT Bit slice 6 */
	PININTBITSLICE7 = 7	/*!< PININT Bit slice 7 */
} PININT_BITSLICE_T;

/**
 * LPC8xx Pin Matching Interrupt bit slice configuration enum values
 */
typedef enum PININT_BITSLICE_CFG {
    PININT_PATTERNCONST1           = 0x0,	/*!< Contributes to product term match */
    PININT_PATTERNRISING           = 0x1,	/*!< Rising edge */    
    PININT_PATTERNFALLING          = 0x2,	/*!< Falling edge */    
    PININT_PATTERNRISINGRFALLING   = 0x3,	/*!< Rising or Falling edge */    
    PININT_PATTERNHIGH             = 0x4,	/*!< High level */    
    PININT_PATTERNLOW              = 0x5,	/*!< Low level */    
    PININT_PATTERCONST0            = 0x6,	/*!< Never contributes for match */    
    PININT_PATTEREVENT             = 0x7	/*!< Match occurs on event */    
} PININT_BITSLICE_CFG_T;

/**
 * @brief	Configure the pins as edge sensitive in Pin interrupt block 
 * @param	pPININT	: The base address of Pin interrupt block 
 * @param	pins	: Pins (ORed value of PININTCH*)
 * @return	Nothing
 */
void PININT_SetPinModeEdge(LPC_PIN_INT_Type *pPININT, uint32_t pins);

/**
 * @brief	Configure the pins as level sensitive in Pin interrupt block 
 * @param	pPININT	: The base address of Pin interrupt block 
 * @param	pins	: Pins (ORed value of PININTCH*)
 * @return	Nothing
 */
void PININT_SetPinModeLevel(LPC_PIN_INT_Type *pPININT, uint32_t pins);

/**
 * @brief	Return current PININT rising edge or high level interrupt enable state
 * @param	pPININT	: The base address of Pin interrupt block 
 * @return	A bifield containing the high edge/level interrupt enables for each
 * interrupt. Bit 0 = PININT0, 1 = PININT1, etc.
 * For each bit, a 0 means the high edge/level interrupt is disabled, while a 1
 * means it's enabled.
 */
uint32_t PININT_GetHighEnabled(LPC_PIN_INT_Type *pPININT);

/**
 * @brief	Enable high edge/level PININT interrupts for pins
 * @param	pPININT	: The base address of Pin interrupt block 
 * @param	pins	: Pins to enable (ORed value of PININTCH*)
 * @return	Nothing
 */
void PININT_EnableIntHigh(LPC_PIN_INT_Type *pPININT, uint32_t pins);

/**
 * @brief	Disable high edge/level PININT interrupts for pins
 * @param	pPININT	: The base address of Pin interrupt block 
 * @param	pins	: Pins to disable (ORed value of PININTCH*)
 * @return	Nothing
 */
void PININT_DisableIntHigh(LPC_PIN_INT_Type *pPININT, uint32_t pins);

/**
 * @brief	Return current PININT falling edge or low level interrupt enable state
 * @param	pPININT	: The base address of Pin interrupt block 
 * @return	A bifield containing the low edge/level interrupt enables for each
 * interrupt. Bit 0 = PININT0, 1 = PININT1, etc.
 * For each bit, a 0 means the low edge/level interrupt is disabled, while a 1
 * means it's enabled.
 */
uint32_t PININT_GetLowEnabled(LPC_PIN_INT_Type *pPININT);
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

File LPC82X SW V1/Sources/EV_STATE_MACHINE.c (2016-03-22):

/****************************************************************************
	Luka Penger 2015
	EV STATE MACHINE
****************************************************************************/

#include "EV_STATE_MACHINE.h"
#include "cmsis_os.h"
#include "SETTINGS.h"

EvModuleMode selectedModuleMode = kEvModuleModeAuto;

extern float proximityVoltage; // 0.0V - 3.3V
extern float pilotPositiveVoltage; // 0.0V - 12.0V
extern float pilotNegativeVoltage; // 0.0V - -12.0V

void (*currentStateMachine)(void) = EV_State_A1;

extern bool pwmRunning;
extern float evPwmDutyCycle;
int evStateMachineWaitMs = 0;
extern int ledWaitMs;
bool manualStartChargingFlag = false;

extern SETTINGS_Struct settingsData;
extern float selectedMaximumCurrent;

void EV_State_Machine(void) {
	if (pilotPositiveVoltage < EV_STATE_A_THRES_HIGH && pilotPositiveVoltage > EV_STATE_A_THRES_LOW) {
		if (currentStateMachine != EV_State_A1) {
			EV_State_A1();
		}
	} else if (pilotPositiveVoltage < EV_STATE_B_THRES_HIGH && pilotPositiveVoltage > EV_STATE_B_THRES_LOW) {
		if (currentStateMachine == EV_State_B1) {
			if (evStateMachineWaitMs == 0 && EV_INPUTS_GetStateSwitchStartCharging() && EV_INPUTS_GetStateSwitchLockDevice()) {
				if ((selectedModuleMode == kEvModuleModeManual && manualStartChargingFlag) || selectedModuleMode == kEvModuleModeAuto) {
					EV_State_B2();
				}
			}
		} else if (currentStateMachine != EV_State_B1 && currentStateMachine != EV_State_B2) {
			EV_State_B1();
			
			evStateMachineWaitMs = 2000;
		}
	} else if (pilotPositiveVoltage < EV_STATE_C_THRES_HIGH && pilotPositiveVoltage > EV_STATE_C_THRES_LOW) {
		if (currentStateMachine == EV_State_B1) {
			if (evStateMachineWaitMs == 0 && EV_INPUTS_GetStateSwitchStartCharging() && EV_INPUTS_GetStateSwitchLockDevice()) {
				if ((selectedModuleMode == kEvModuleModeManual && manualStartChargingFlag) || selectedModuleMode == kEvModuleModeAuto) {
					EV_State_B2();
				}
			}
		} else if (currentStateMachine != EV_State_C1 && currentStateMachine != EV_State_C2) {
			if (currentStateMachine == EV_State_B2) {
				EV_State_C2();
			} else if ((EV_INPUTS_GetStateSwitchStartCharging() && EV_INPUTS_GetStateSwitchLockDevice())) {
				EV_State_C2();
			} else if (selectedModuleMode == kEvModuleModeAuto && (currentStateMachine == EV_State_A1 || currentStateMachine == EV_State_A2)) {
				EV_State_B1();
			}
		}
	} else if (pilotPositiveVoltage < EV_STATE_D_THRES_HIGH && pilotPositiveVoltage > EV_STATE_D_THRES_LOW) {
		if (currentStateMachine == EV_State_B1) {
			if (evStateMachineWaitMs == 0 && EV_INPUTS_GetStateSwitchStartCharging() && EV_INPUTS_GetStateSwitchLockDevice()) {
				if ((selectedModuleMode == kEvModuleModeManual && manualStartChargingFlag) || selectedModuleMode == kEvModuleModeAuto) {
					EV_State_B2();
				}
			}
		} else if (currentStateMachine != EV_State_D1 && currentStateMachine != EV_State_D2) {
			if (currentStateMachine == EV_State_C2) {
				EV_State_D2();
			} else if ((EV_INPUTS_GetStateSwitchStartCharging() && EV_INPUTS_GetStateSwitchLockDevice())) {
				EV_State_D2();
			} else if (selectedModuleMode == kEvModuleModeAuto && (currentStateMachine == EV_State_A1 || currentStateMachine == EV_State_A2)) {
				EV_State_B1();
			}
		}
	}
	
	if (pwmRunning && pilotNegativeVoltage < EV_STATE_F_THRES_HIGH && pilotNegativeVoltage < EV_STATE_F_THRES_LOW) {
		if (currentStateMachine != EV_State_F) {
			EV_State_F();
			
			evStateMachineWaitMs = 30000;
		}
	} else if (pilotPositiveVoltage >= EV_STATE_E_THRES_LOW && pilotPositiveVoltage < EV_STATE_E_THRES_HIGH) {
		if (currentStateMachine != EV_State_E) {
			EV_State_E();
			
			evStateMachineWaitMs = 30000;
		}
	}
	
	if (currentStateMachine == EV_State_E || currentStateMachine == EV_State_F) {
		if (evStateMachineWaitMs == 0) {
			EV_State_A1();
		}
	}
}

// States

void EV_State_A1(void) {
	currentStateMachine = EV_State_A1;

	if (pwmRunning) EV_PWM_Stop();
	
	EV_OUTPUTS_SetPower(false);
	EV_OUTPUTS_SetVentilation(false);
	EV_OUTPUTS_SetShut(false);
	
	ledWaitMs = 0;
	manualStartChargingFlag = false;
}

void EV_State_A2(void) {
	currentStateMachine = EV_State_A2;
	
	if (!pwmRunning) EV_PWM_Start();
	
	EV_OUTPUTS_SetPower(false);
	EV_OUTPUTS_SetVentilation(false);
	EV_OUTPUTS_SetShut(false);
	
	ledWaitMs = 0;
	manualStartChargingFlag = false;
}

void EV_State_B1(void) {
	float value = 0.0f;
	
	currentStateMachine = EV_State_B1;
	
	if (settingsData.enableProximity > 0) {
		value = EV_PWM_CheckProximityMaxCurrent(proximityVoltage);
		
		if (value <= selectedMaximumCurrent) {
			EV_PWM_SetDutyCycle(EV_PWM_CheckProximityMaxCurrent(proximityVoltage));
		}
	}
	
	if (pwmRunning) EV_PWM_Stop();
	
	EV_OUTPUTS_SetPower(false);
	EV_OUTPUTS_SetVentilation(false);
	EV_OUTPUTS_SetShut(true);
	
	ledWaitMs = 0;
	manualStartChargingFlag = false;
}

void EV_State_B2(void) {
	currentStateMachine = EV_State_B2;
	
	if (!pwmRunning) EV_PWM_Start();
	
	EV_OUTPUTS_SetPower(false);
	EV_OUTPUTS_SetVentilation(false);
	EV_OUTPUTS_SetShut(true);
	
	ledWaitMs = 0;
	manualStartChargingFlag = false;
}

void EV_State_C1(void) {
	currentStateMachine = EV_State_C1;
	
	if (pwmRunning) EV_PWM_Stop();
	
	EV_OUTPUTS_SetPower(false);
	EV_OUTPUTS_SetVentilation(false);
	EV_OUTPUTS_SetShut(true);
	
	ledWaitMs = 0;
	manualStartChargingFlag = false;
}

void EV_State_C2(void) {
	currentStateMachine = EV_State_C2;
	
	if (!pwmRunning) EV_PWM_Start();
	
	EV_OUTPUTS_SetPower(true);
	EV_OUTPUTS_SetVentilation(false);
	EV_OUTPUTS_SetShut(true);
	
	ledWaitMs = 0;
	manualStartChargingFlag = false;
}

void EV_State_D1(void) {
	currentStateMachine = EV_State_D1;
	
	if (pwmRunning) EV_PWM_Stop();
	
	EV_OUTPUTS_SetPower(false);
	EV_OUTPUTS_SetVentilation(true);
	EV_OUTPUTS_SetShut(true);
	
	ledWaitMs = 0;
	manualStartChargingFlag = false;
}

void EV_State_D2(void) {
	currentStateMachine = EV_State_D2;
	
	if (!pwmRunning) EV_PWM_Start();
	
	EV_OUTPUTS_SetPower(true);
	EV_OUTPUTS_SetVentilation(true);
	EV_OUTPUTS_SetShut(true);
	
	ledWaitMs = 0;
	manualStartChargingFlag = false;
}

void EV_State_E(void) {
	currentStateMachine = EV_State_E;
	
	if (pwmRunning) EV_PWM_Stop();
	
	EV_OUTPUTS_SetPower(false);
	EV_OUTPUTS_SetVentilation(false);
	EV_OUTPUTS_SetShut(false);
	
	ledWaitMs = 0;
	manualStartChargingFlag = false;
}

void EV_State_F(void) {
	currentStateMachine = EV_State_F;
	
	if (pwmRunning) EV_PWM_Stop();
	
	EV_OUTPUTS_SetPower(false);
	EV_OUTPUTS_SetVentilation(false);
	EV_OUTPUTS_SetShut(false);
	
	ledWaitMs = 0;
	manualStartChargingFlag = false;
}

void EV_DisableAllOutputs(void) {
	currentStateMachine = EV_State_A1;
	
	if (pwmRunning) EV_PWM_Stop();
	
	EV_OUTPUTS_SetPower(false);
	EV_OUTPUTS_SetVentilation(false);
	EV_OUTPUTS_SetShut(false);
	
	ledWaitMs = 0;
	manualStartChargingFlag = false;
}

/****************************************************************************
                            End Of File
****************************************************************************/

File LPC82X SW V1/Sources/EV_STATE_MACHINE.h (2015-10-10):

/****************************************************************************
	Luka Penger 2015
	EV STATE MACHINE
****************************************************************************/
#ifndef __EV_STATE_MACHINE_H 
#define __EV_STATE_MACHINE_H

#include <lpc_types.h>
#include "EV_ADC.h"
#include "EV_PWM.h"
#include "EV_OUTPUTS.h"
#include "EV_INPUTS.h"
#include "HELP.h"

#define EV_STATE_A_THRES_HIGH						13.0  // Volts
#define EV_STATE_A_THRES_LOW						11.0  // Volts

#define EV_STATE_B_THRES_HIGH						10.0  // Volts
#define EV_STATE_B_THRES_LOW						8.0  // Volts

#define EV_STATE_C_THRES_HIGH						7.0  // Volts
#define EV_STATE_C_THRES_LOW						5.0  // Volts

#define EV_STATE_D_THRES_HIGH						4.0  // Volts
#define EV_STATE_D_THRES_LOW						2.0  // Volts

#define EV_STATE_E_THRES_HIGH						1.0	// Volts
#define EV_STATE_E_THRES_LOW						-1.0	// Volts

#define EV_STATE_F_THRES_HIGH						-13.0	// Volts
#define EV_STATE_F_THRES_LOW						-11.0	// Volts

typedef enum {
	kEvModuleModeAuto,
	kEvModuleModeManual
} EvModuleMode;

void EV_State_Machine(void);

void EV_State_A1(void);
void EV_State_A2(void);
void EV_State_B1(void);
void EV_State_B2(void);
void EV_State_C1(void);
void EV_State_C2(void);
void EV_State_D1(void);
void EV_State_D2(void);
void EV_State_E(void);
void EV_State_F(void);
void EV_DisableAllOutputs(void);

#endif // end __EV_STATE_MACHINE_H
/****************************************************************************
                            End Of File
****************************************************************************/

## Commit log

2015-11-24 Added PCB V2
    [PCB_V2.sch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]
2015-12-27 ADC Fixed + commands updated
    [EV_ADC.c, EV_PWM.c, EV_STATE_MACHINE.c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]
2016-01-09 Added Watchdog timer
2016-01-14 Update TYPE_2_CONTROLLER_LPC824_V1_KEIL5.c
    Fix stop charging and module mode
    [TYPE_2_CONTROLLER_LPC824_V1_KEIL5.c]
2016-01-14 Removed stop charging for module mode change
2016-03-22 fix protocol + added proximity function
    [EV_ADC.c, EV_PWM.c, EV_PWM.h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]
